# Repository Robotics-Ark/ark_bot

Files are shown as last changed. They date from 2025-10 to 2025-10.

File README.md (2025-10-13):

<h1 align="center">
🥳 Ark_Bot 🥳
</h1>

> **Handbook**  
> Version: `v1.0.0` • Date: `<2025-10>` • Author: `Harry Warriner / Ark`

---

<div align = "center">
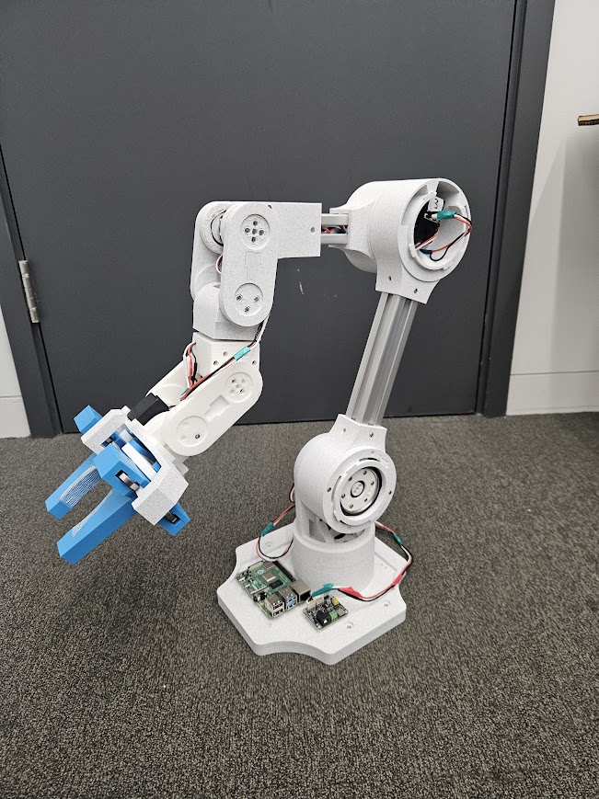
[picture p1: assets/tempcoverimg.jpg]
Cover Image

</div>

## Table of Contents

- [1. Overview](#1-overview)
- [2. Example Videos](#2-example-videos)
- [3. Bill of Materials](#3-bill-of-materials)
- [4. Required Tools](#4-required-tools)
- [5. List of 3D Parts](#5-list-of-3d-parts)

- [6. Specifications](#6-specifications)
- [7. Before You Start](#7-before-you-start)
- [8. Assembly Guide](#8-assembly-guide)

- [9. Motor Configuration](#9-motor-configuration)
- [10. Software Setup](#10-software-setup)
- [11. Calibration](#11-calibration)

- [12. Operation](#12-operation)
- [13. Troubleshooting](#13-troubleshooting)
- [14. FAQ](#14-faq)

---

## 1. Overview

**Purpose:** ArkBot is designed to be an affordable high strength, high accuracy robotic arm you can build at home.  
**Scope:** This handbook covers how to build ArkBot and how to get it running within the Ark Framework.

The ArkBot is a pick-and-place robotic arm designed to be affordable and easy to build at home. With the intention of demonstrating the <a href="https://github.com/Robotics-Ark/ark_framework">ark_framework's</a> capabilities. Comes complete with an accurate URDF file. <br>

<table align="center">
  <tr>
    <td align="center" style="border: none;">
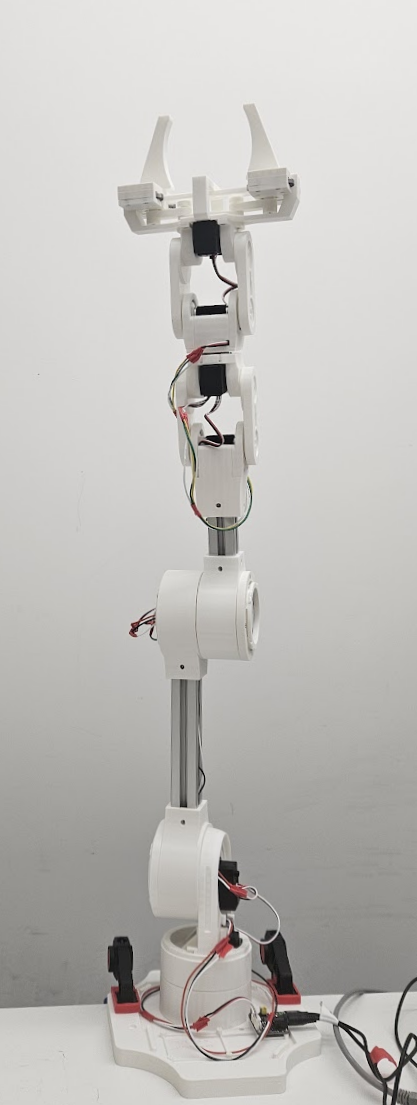
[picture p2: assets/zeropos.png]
      
    </td>
    <td align="center" style="border: none;">
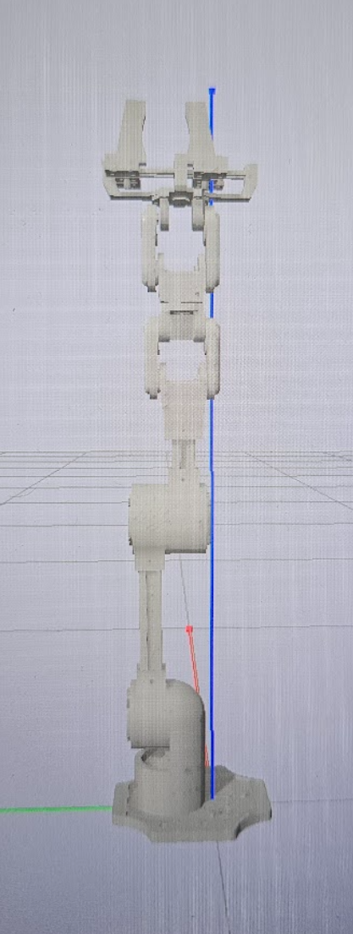
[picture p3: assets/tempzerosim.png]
      
    </td>
  </tr>
</table>

---

## 2. Example videos

<table>
<tr>
<td >Pick and Place</td>
<td >
  TPU Gripper Example
</td>
<td >Short IK Example</td>

</tr>
</table>

## 3. Bill of Materials.

The parts ordered from either side (amazon or cheapest) are the same parts, the difference is the time and price. The amazon links will come significantly faster whilst the others will take a while longer.
At the bottom though there are two different PLA filaments, the bambu or an equivalent high brand printer filament is reccomended, but if on a budget, the amazon ones will work fine.

| Totals | Amazon Total: | Cheapest Total: |
| --- | --- | --- |
| | £348.12 | £215.86 |

<hr>

<div align = "center" >

| Qty Needed | Name | Amazon Price | Amazon Link | Cheapest Price | Cheapest Link |
| --- | --- | --- | --- | --- | --- |
| 7 | ST 3215 Servos | £26.99 (x7)  | [Amazon](https://www.amazon.co.uk/Waveshare-Servo-Precision-Programmable-Switchable/dp/B0B6HSBRGF) | £20.10 (x7) | [Robotshop](https://uk.robotshop.com/products/waveshare-30kg-serial-bus-servo-high-precision-torque-w-360-deg-encoder) |
| 1 | Servo Bus Driver | £9.99 (x1) | [Amazon](https://www.amazon.co.uk/Waveshare-Integrates-Control-Applicable-Integrate/dp/B0CJ6TP3TP) | £4.80 (x1) | [PiHut](https://thepihut.com/products/serial-bus-servo-driver-board) |
| 36 | 693-2z (Tiny Bearings) | £9.89 (x2) | [Amazon](https://www.amazon.co.uk/sourcing-map-Groove-Bearing-Bearings/dp/B07FXVZ4W4) | £2.31 (x4) | [AliExpress](https://www.aliexpress.com/item/1005005858463502.html) |
| 12 | 6802-2RS (Medium Bearings)  | £9.79 (x2) | [Amazon](https://www.amazon.co.uk/dp/B07FXY8YHK) | £3.23 (x2) | [AliExpress](https://www.aliexpress.com/item/1005006082431261.html) |
| 5 | 6706-2RS (Big Bearings) | £12.19 (x1)  | [Amazon](https://www.amazon.co.uk/sourcing-map-30x37x4mm-Precision-Lubricated/dp/B0D6WJX2K5) | £1.27 (x5) | [AliExpress](https://www.aliexpress.com/item/1005003619960721.html) |
| 6 | 6810-2RS (Massive Bearings) | £26.29 (x1)  | [Amazon](https://www.amazon.co.uk/sourcing-map-50x65x7mm-Precision-Lubricated/dp/B0D728SYYT) | £10.39 (x1) | [AliExpress](https://www.aliexpress.com/item/32842423917.html) |
| 1 | 10cm 30x30 Aluminium Extr.  | £2.27 (x1) | [Amazon](https://www.aluminium-profile.co.uk/30x30-aluminium-profile-kjn990720/) | £2.27 (x1) | [Aluminium-Profile](https://www.aluminium-profile.co.uk/30x30-aluminium-profile-kjn990720/) |
| 1 | 20cm 30x30 Aluminium Extr.  | £3.35 (x1) | [Amazon](https://www.aluminium-profile.co.uk/30x30-aluminium-profile-kjn990720/) | £3.35 (x1) | [Aluminium-Profile](https://www.aluminium-profile.co.uk/30x30-aluminium-profile-kjn990720/) |
| 12 | M3 30x30 T-nuts (100) | £7.89 (x1) | [Amazon](https://www.amazon.co.uk/sourcing-map-Fastener-Aluminum-Accessories/dp/B0D5XK6SL1) | £3.46 (x1) | [AliExpress](https://www.aliexpress.com/item/1005005553086770.html) |
| 1 | Box of M3 Screws | £7.88 (x1) | [Amazon](https://www.amazon.co.uk/Assortment-Stainless-Replacement-Machine-Fastener/dp/B0B3MGZ7T2) | £7.88 (x1) | [Amazon](https://www.amazon.co.uk/Assortment-Stainless-Replacement-Machine-Fastener/dp/B0B3MGZ7T2) |
| 50 | Threaded Inserts (100) | £7.99 (x1) | [Amazon](https://www.amazon.co.uk/HANGLIFE-Threaded-Inserts-Printing-Components/dp/B0CS6VZYL8) | £0.98 (x1) | [AliExpress](https://www.aliexpress.com/item/1005008666672949.html) |
| 2 | 1kg of PLA | £20.99 (x2)  | [BambuLab](https://uk.store.bambulab.com/products/pla-basic-filament) | £9.99 (x2) | [Amazon](https://www.amazon.co.uk/PLA-Filament-Tolerance-Materials-Compatible/dp/B0DCJ7TTDK) |

</div>

---

## 4. Required Tools

This is a list of the most basic tools required to build the Ark_bot, additionally it is reccomended to have a drill and pliers, just to improve quality of assembly.

<div align="center">

| List of tools Required  |
| ----------------------- |
| 3D printer              |
| Soldering Iron          |
| 5mm 12v DC power supply |
| m3 Hex Key              |
| wire cutters            |
| electrical tape         |
| electrical wires        |
| Clamps                  |

</div>

---

## 5. List of 3D parts

> Release `v1.0.0` Parts List (Grouped by Subsystem)

<div align="center">

| **Base** | **Cyclodial Drive** | **Links** | **Claw** | **Limbs** |
| --- | --- | --- | --- | --- |
| 1 × Base | 2 × Motor Holders | 1 × Link 3 Body | 2 × Claw Connector | 2 × Limb Motor Side |
| 2 × Base Bearing Cover | 2 × Bearing Holder Disk (Exterior) | 2 × Link3 and 5 Motor Side | 1 × Claw Bottom Case | 2 × Limb Non Motor Side |
| 1 × Base Motor Holder | 2 × Cyclodial Drive Exterior | 2 × Link3 and 5 Side | 1 × Claw Runners | |
| 1 × Joint 1 Base | 2 × Cyclodial Drive Exterior Top | 1 × Link4 | 2 × Claw Body | |
| 1 × Joint 1 Connector to Joint 2 | 1 × Cyclodial Drive Other Half | 1 × Link5 Body | 4 × Claw Runner Clamp | |
| | 3 × Eccentric Rod Motor Connector | | 2 × Claw Link | |
| | 18 × Internal Cyclodial Drive Spacer | | 2 × Finger | |
| | 6 × Cyclodial Disk | | 1 × Claw Motor Driver | |
| | 3 × Cyclodial Driver Interior Top | | 2 × Claw Motor Holder Link Pin | |
| | 3 × Eccentric Rod Middle | | 2 × Claw Link Motor | |
| | 3 × Eccentric Rod Top | | 2 × Claw Link Cap | |
| | 3 × Cyclodial Driver Interior Bottom | | | |

---

**Total Parts: 86**

</div>

---

## 6. Specifications

| Parameter | Value  |
| --- | --- |
| Reach | 1 m |
| Weight | 2.6 kg |
| Payload | 1.8kg  |
| DOF | 6 |
| Input Voltage | DC12V  |

---

## 7. Before You Start

When 3D printing, the Cyclodial Disks, ensure that the diameter of the 6 holes on the outside are exactly 12mm in diamter, and that the disk fits near perfectly in the exterior.

<div align = "center">
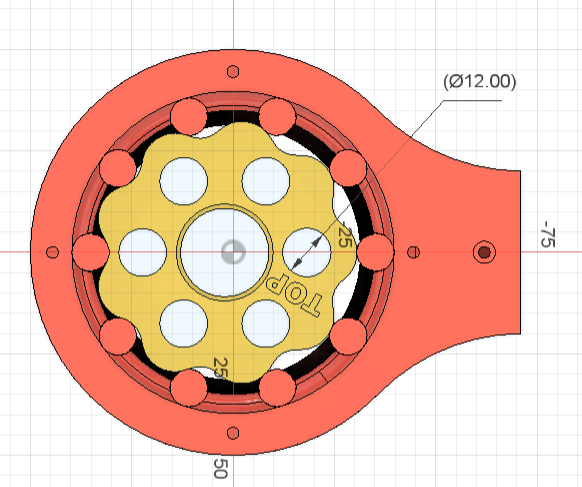
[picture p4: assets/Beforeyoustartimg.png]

</div>

The better the fit the more accurate the final positioning will be.

> This is the only note with the 3D prininting, as long as these two parts work. Everything else can be printed on random settings, of course the higher the infill the stronger the final parts.

---

## 8. Assembly Guide

> ⏱ **Total time:** <estimate, 120 minutes>  
> 🧰 **Skill level:** Intermediate
<div align="center">
  
Assembly (https://www.youtube.com/watch?v=Kuk4pC0EaEw)

If clicking the above video did not work, click [here](https://www.youtube.com/watch?v=Kuk4pC0EaEw)

</div>
---

## 9. Motor Configuration

Connect the indivual motor to the driver board.

Go to the configuration.py file in arkbot. <a href="arkbot\Configuration.py">Config file</a>

Make sure the config is correct in the file:

```python
if __name__ == "__main__":
    DEVICENAME = "COM7"       # or "/dev/ttyUSB0"
    BAUDRATE   = 1_000_000
```

Then run the program, it will tell you the ID number of the motor, if this is not correct, change it to the number associated to that motor.

---

## 10. Software Setup

### Ark Framework

Go to the Ark Framework repo and follow the instructions there.

Make sure Ark Registry is running.

Make sure arkbot.py is also running (in a different terminal)

Then use the jupyter notebook in tests, if using sim, make sure sim_node.py is running. And that sim=true in the config of the jupyter notebook.

**Configure:**
Make sure the port is correct in the .yaml file.

```json
{
  real_config:
        port: "/dev/ttyACM0"
        baudrate: 1000000
}
```

---

## 11. Calibration

You should be able to carefully move the cyclodial drives and the motors when powered off. Move ArkBot so that it is completly facing upwards, and plug it in. Run the configuration.py file, and when promted set all the midpoint positions.

Power cycle the robotic arm, and run the configuration code, and when promted go to output and read the current ticks of all the motors. These then need to be put into the arkbot.yaml file:

```json
home_ticks:
          {
            "1": 2800,
            "2": 2431,
            "3": 2093,
            "4": 2050,
            "5": 2059,
            "6": 2020,
            "7": 1011,
          }
```

Next is the home loop configuration. The robotic arm must start from the position below. (Only matters for the first 3 motors) These motors rotate multiple times due to the gear ratio. Therefore the loops to get the [0,0,0,...] position must also be inputted:

```json
home_loops: {
    "1": 0, "2": 3, "3": 3, "4": 0, "5": 0, "6": 0, "7": 0
    }
```

Now run the jupyter notebook and send it to [0,0,0,...] if it goes straight up then the calibration was a succsess.

Cover Image

> ✅ **Pass criteria:** When sent to [0,0,0,...] it goes straight up

---

## 12. Operation

- Ensure that it is in the starting position.
- Power on and send to home.
- If succseful, enjoy using ArkBot!

---

## 13. Troubleshooting

| Symptom | Possible Causes | Fix |
| --- | --- | --- |
| Won’t power on | 12V Cable Not Plugged in | Plug it in |
| Jittery motion | Cyclodial disks not correct size | Reprint to size |
| Massive Backlash | Plastic could have worn and snapped | Reprint parts |

---

## 14. FAQ

**Q:**
**A:**

**Q:**
**A:**

---

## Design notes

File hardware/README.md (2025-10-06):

# 3D Assets

## Excel Spreadsheet
There is an Excel spreadsheet which can be downloaded and used as a checklist for all the 3D models

## External 3D assets used
Links to any websites which was used for external 3D assets.

### Traceparts
Used for Aluminium Profile Extrusions
<!-- *[TraceParts](https://www.traceparts.com/en)* -->

<!-- *[20x20 Profile](https://www.traceparts.com/en/product/dongguan-forrun-hardware-co-ltd-20-series-aluminium-alloy-profiles-20x20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)* -->
*[30x30 Profile](https://www.traceparts.com/en/product/dongguan-forrun-hardware-co-ltd-30-series-aluminium-alloy-profiles-30x30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)*

### Astbearings
USed for Bearings

*[6706-2RS Bearing](https://www.astbearings.com/catalog/root/6706-2RS)*

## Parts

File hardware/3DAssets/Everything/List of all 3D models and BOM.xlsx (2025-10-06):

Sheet: 3D models
Release V1.0
 | Quanity | Name of File
 | 1 | Base
 | 2 | Base Bearing Cover
 | 1 | Base Motor Holder
 | 1 | Joint 1 Base
 | 1 | Joint 1 Connector to Joint 2
 | 2 | Motor Holders
 | 2 | Bearing Holder Disk for cyclodial Drive exterior | Bill of Materials In the other sheet
 | 2 | Cyclodial Drive Exterior
 | 2 | Cyclodial Drive Exterior Top
 | 1 | Cyclodial Drive Other Half
 | 3 | Eccentric Rod Motor Connector
 | 18 | Internal Cyclodial drive Spacer
 | 6 | Cyclodial Disk
 | 3 | Cyclodial Driver Interior Top
 | 3 | Eccentric Rod Middle
 | 3 | Eccentric Rod Top
 | 3 | Cyclodial Driver Interior Bottom
 | 1 | Link 3 Body
 | 2 | Link3 and 5 Motor Side
 | 2 | Link3 and 5 Side
 | 1 | Link4
 | 1 | Link5 Body
 | 2 | Claw Connector
 | 1 | Claw Bottom Case
 | 1 | Claw Runners
 | 2 | Claw Body
 | 4 | Claw Runner Clamp
 | 2 | Claw Link
 | 2 | Finger
 | 1 | Claw Motor Driver
 | 2 | Claw Motor Holder Link PIn
 | 2 | Claw Link Motor
 | 2 | Claw Link Cap
 | 2 | Limb Motor Side
 | 2 | Limb Non Motor Side
Total parts: | 86

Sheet: Bill of Materials
 |  |  | Amazon |  |  |  |  | Cheapest Found
 |  | Quantity in link | Name | Price | Link | Quantiy needed | Quantity in link | Name | Price | Link | Quantity Needed
7 | ST 3215 Servos | 1 | ST 3215 Servos | £26.99 | https://www.amazon.co.uk/Waveshare-Servo-Precision-Programmable-Switchable/dp/B0B6HSBRGF?s=industrial | 7 | 1 | ST 3215 Servos | £20.10 | https://uk.robotshop.com/products/waveshare-30kg-serial-bus-servo-high-precision-torque-w-360-deg-encoder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 | 7
1 | Servo Bus Driver | 1 | Servo Bus Driver | £9.99 | https://www.amazon.co.uk/Waveshare-Integrates-Control-Applicable-Integrate/dp/B0CJ6TP3TP | 1 | 1 | Servo Bus Driver | £4.80 | https://thepihut.com/products/serial-bus-servo-driver-board | 1
36 | 693-2z(or zz) (Tiny Bearings) | 20 | 693-2z(or zz) (Tiny Bearings) | £9.89 | https://www.amazon.co.uk/sourcing-map-Groove-Bearing-Bearings/dp/B07FXVZ4W4?s=amazon-devices | 2 | 10 | 693-2z(or zz) (Tiny Bearings) | £2.31 | https://www.aliexpress.com/item/1005005858463502.html?curPageLogUid=vG9asOPYtleS | 4
12 | 6802-2RS (Medium Bearings | 10 | 6802-2RS (Medium Bearings | £9.79 | https://www.amazon.co.uk/dp/B07FXY8YHK?ref_=ppx_hzsearch_conn_dt_b_fed_asin_title_4&th=1 | 2 | 10 | 6802-2RS (Medium Bearings | £3.23 | https://www.aliexpress.com/item/1005006082431261.html?curPageLogUid=MpFagQTCKDh6 | 2
5 | 6706-2RS (Big Bearings) | 5 | 6706-2RS (Big Bearings) | £12.19 | https://www.amazon.co.uk/sourcing-map-30x37x4mm-Precision-Lubricated/dp/B0D6WJX2K5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 | 1 | 1 | 6706-2RS (Big Bearings) | £1.27 | https://www.aliexpress.com/item/1005003619960721.html?curPageLogUid=VV2sZ14YRMKX | 5
6 | 6810-2RS (Massive Bearings) | 10 | 6810-2RS (Massive Bearings) | £26.29 | https://www.amazon.co.uk/sourcing-map-50x65x7mm-Precision-Lubricated/dp/B0D728SYYT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 | 1 | 10 | 6810-2RS (Massive Bearings) | £10.39 | https://www.aliexpress.com/item/32842423917.html?curPageLogUid=EFcuFxcUSFh2 | 1
1 | 10cm 30x30 Alluminum extrusion | 1 | 10cm 30x30 Alluminum extrusion | £2.27 | https://www.aluminium-profile.co.uk/30x30-aluminium-profile-kjn990720/ | 1 | 1 | 10cm 30x30 Alluminum extrusion | £2.27 | https://www.aluminium-profile.co.uk/30x30-aluminium-profile-kjn990720/ | 1
1 | 20cm 30x30 Alluminum extrusion | 1 | 20cm 30x30 Alluminum extrusion | £3.35 | https://www.aluminium-profile.co.uk/30x30-aluminium-profile-kjn990720/ | 1 | 1 | 20cm 30x30 Alluminum extrusion | £3.35 | https://www.aluminium-profile.co.uk/30x30-aluminium-profile-kjn990720/ | 1
12 | M3 30x30 T-nuts | 100 | M3 30x30 T-nuts | £7.89 | https://www.amazon.co.uk/sourcing-map-Fastener-Aluminum-Accessories/dp/B0D5XK6SL1 | 1 | 20 | M3 30x30 T-nuts | £3.46 | https://www.aliexpress.com/item/1005005553086770.html?curPageLogUid=1GgLfjFOVcWH | 1
1 | Box of generic M3 screws | 1 | Box of generic M3 screws | £7.88 | https://www.amazon.co.uk/Assortment-Stainless-Replacement-Machine-Fastener/dp/B0B3MGZ7T2 | 1 | 1 | Box of generic M3 screws | £7.88 | https://www.amazon.co.uk/Assortment-Stainless-Replacement-Machine-Fastener/dp/B0B3MGZ7T2 | 1
50 | Threaded inserts | 100 | Threaded inserts | £7.99 | https://www.amazon.co.uk/HANGLIFE-Threaded-Inserts-Printing-Components/dp/B0CS6VZYL8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 | 1 | 50 | Threaded inserts | £0.98 | https://www.aliexpress.com/item/1005008666672949.html?curPageLogUid=AIubewLqcBkO | 1
2 | 1kg of PLA | 1 | 1kg of PLA | £20.99 | https://uk.store.bambulab.com/products/pla-basic-filament?id=40589883768892 | 2 | 1 | 1kg of PLA | £9.99 | https://www.amazon.co.uk/PLA-Filament-Tolerance-Materials-Compatible/dp/B0DCJ7TTDK | 2
 |  |  |  | Total Price from amazon |  |  |  |  | Total Price from cheapsource
 |  |  |  | £348.12 |  |  |  |  | £215.86

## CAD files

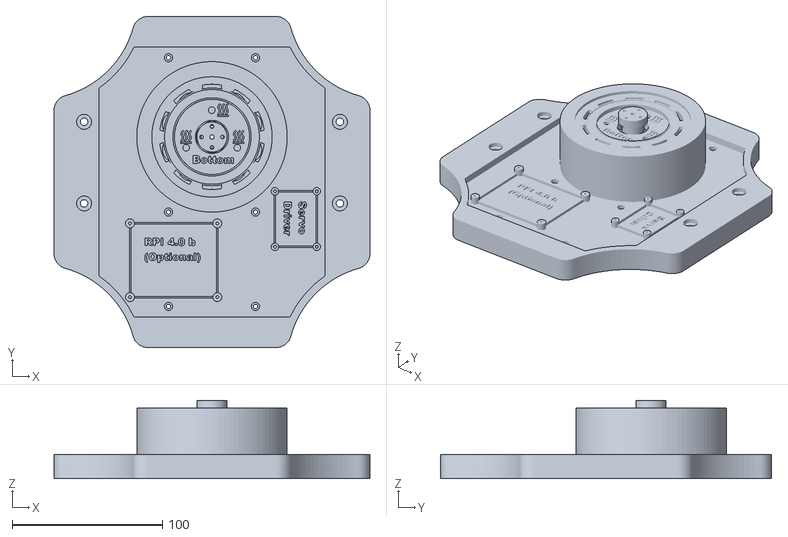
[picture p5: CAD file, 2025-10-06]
arkbot/meshes/collision/base_link.stl
210.0 x 220.0 x 52.0

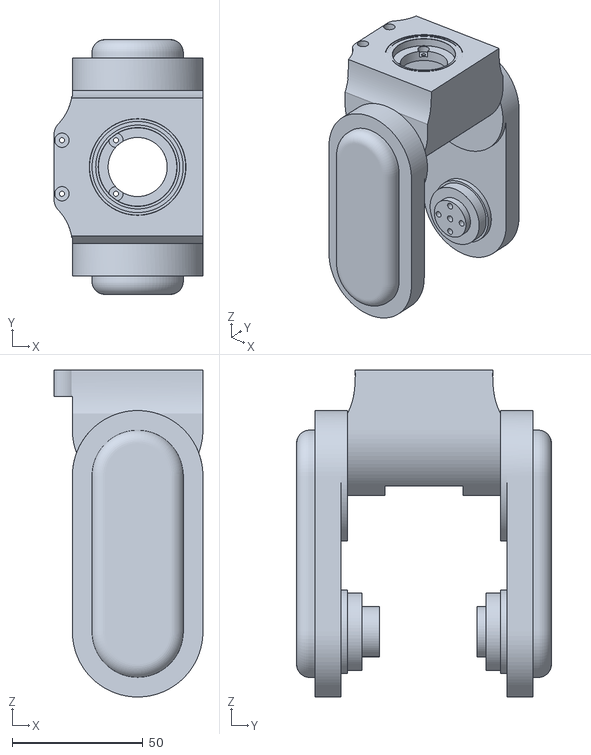
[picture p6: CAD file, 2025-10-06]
arkbot/meshes/visual/link4_v2_1.stl
57.0 x 97.6 x 125.2

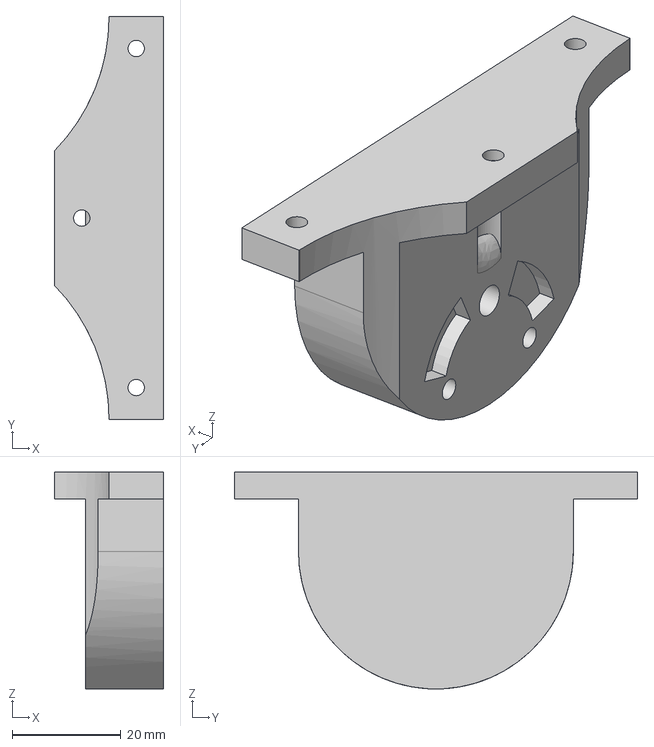
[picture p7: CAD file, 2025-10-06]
hardware/3DAssets/Everything/Claw Connector.step
20.0 x 74.0 x 39.8 mm

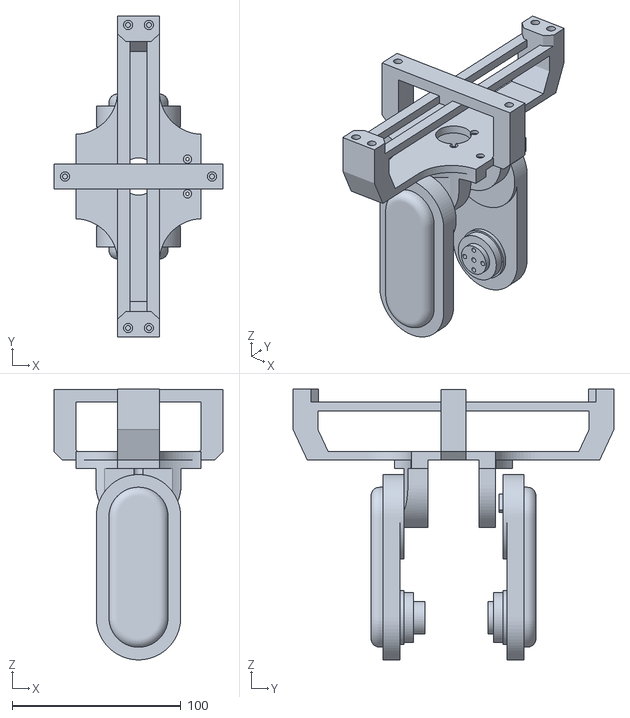
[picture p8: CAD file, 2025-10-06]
hardware/URDF/meshes/collision/Hand_v2_1.stl
100.0 x 190.0 x 160.2

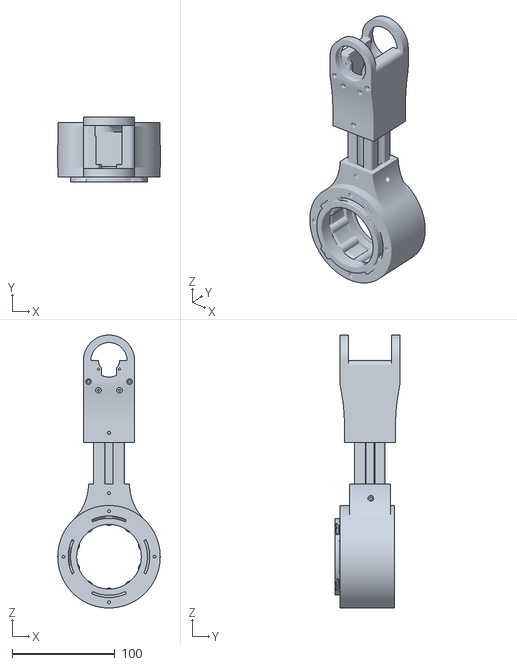
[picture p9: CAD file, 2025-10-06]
hardware/URDF/meshes/visual/link3_v2_1.stl
100.0 x 63.4 x 266.3

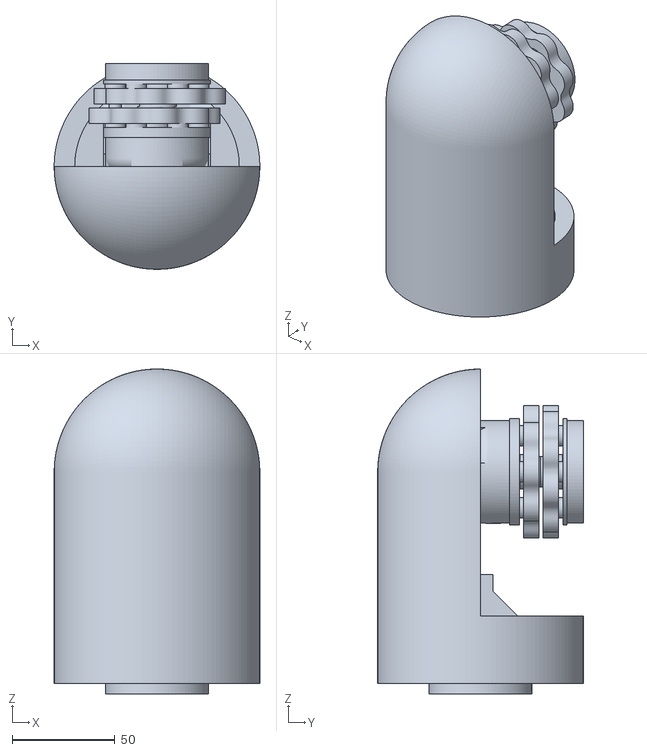
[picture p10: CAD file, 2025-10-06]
arkbot/meshes/collision/Link1_v2_1.stl
100.0 x 100.0 x 158.0

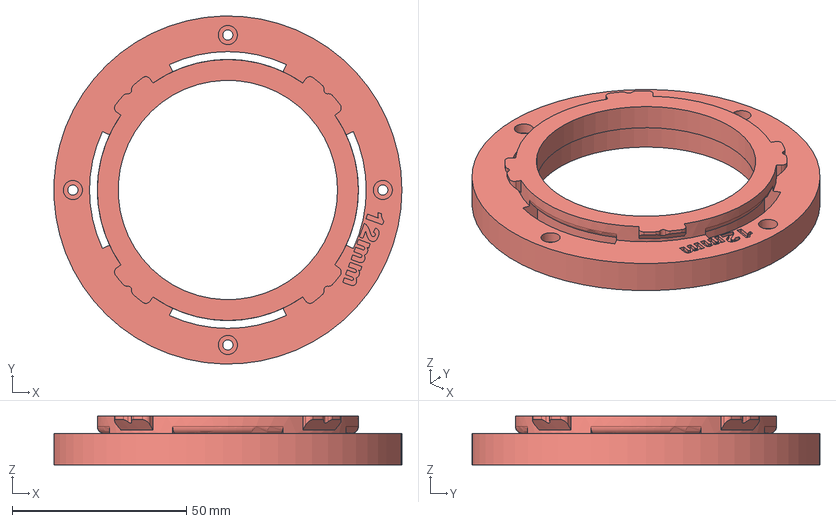
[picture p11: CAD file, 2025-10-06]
hardware/3DAssets/Everything/Cyclodial Drive Exterior Top.step
99.9 x 100.0 x 14.0 mm

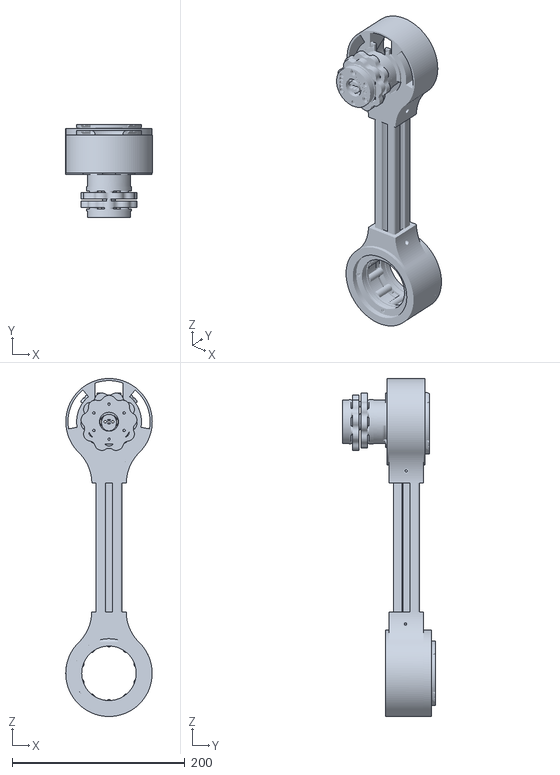
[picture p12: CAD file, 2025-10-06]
hardware/URDF/meshes/collision/link2_v2_1.stl
100.1 x 108.1 x 391.1

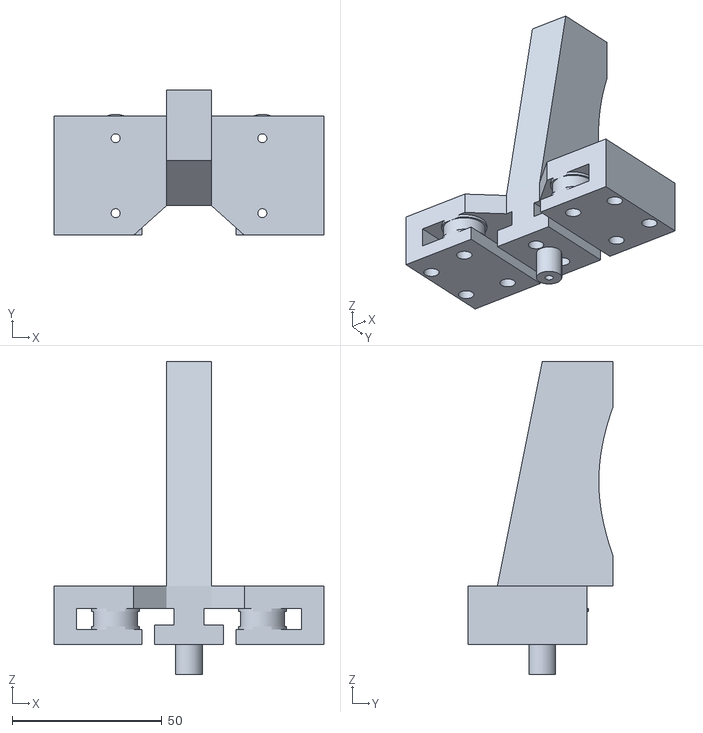
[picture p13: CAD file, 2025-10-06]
hardware/URDF/meshes/visual/finger_v2__1__1.stl
90.0 x 48.6 x 104.5

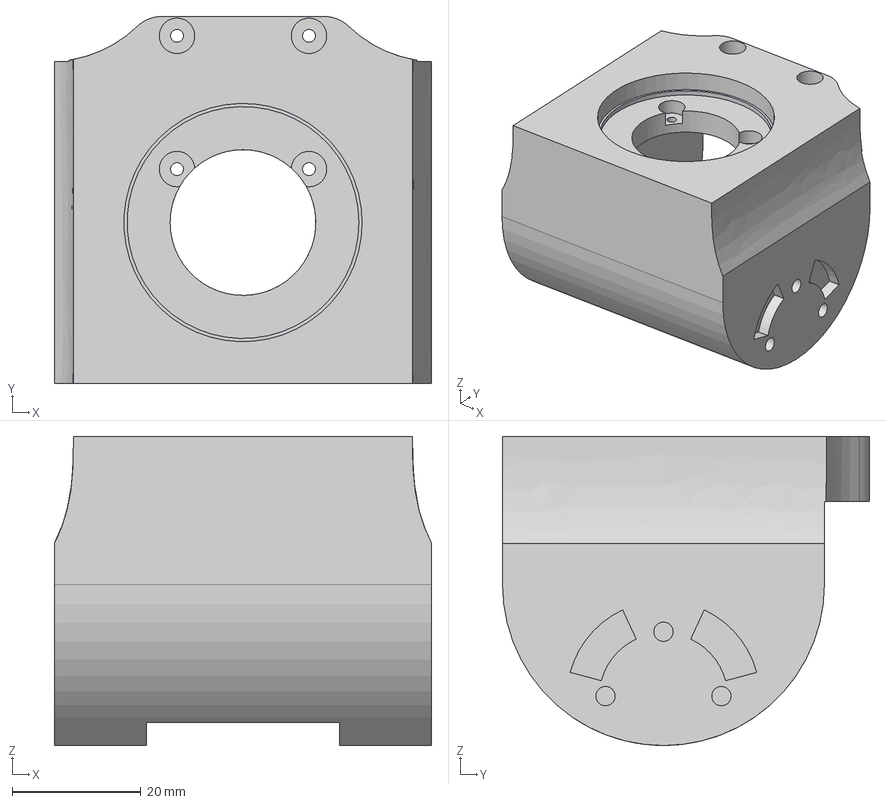
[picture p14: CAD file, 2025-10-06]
hardware/3DAssets/Everything/Link4.step
58.6 x 57.0 x 48.0 mm

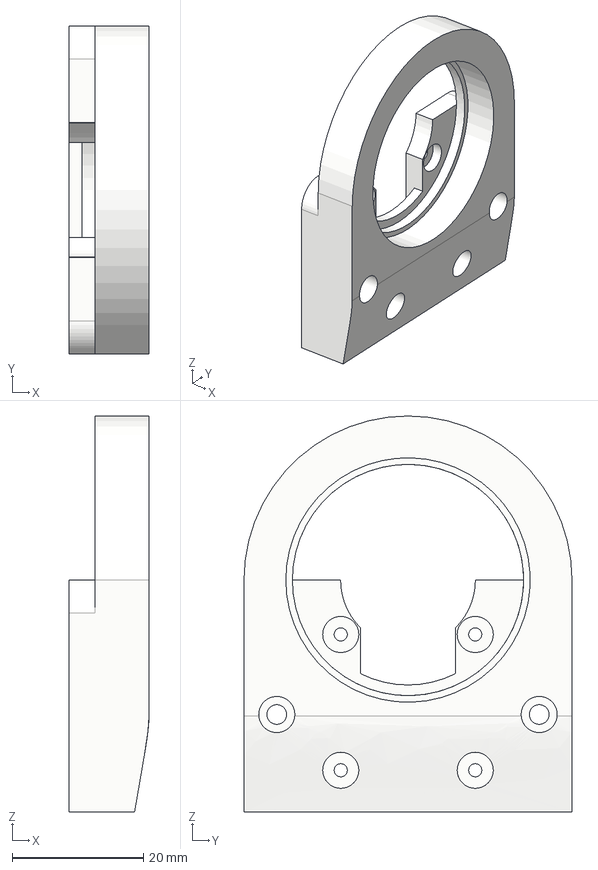
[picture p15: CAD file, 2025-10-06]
hardware/3DAssets/Everything/Link3 and 5 Motor Side.step
12.2 x 50.0 x 60.4 mm

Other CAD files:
arkbot/meshes/collision/finger_v2_1.stl
arkbot/meshes/collision/link5_v2_1.stl
arkbot/meshes/visual/finger_v2_1.stl
arkbot/meshes/visual/link5_v2_1.stl
hardware/3DAssets/Everything/Base Bearing Cover.step
hardware/3DAssets/Everything/Base Motor Holder.step
hardware/3DAssets/Everything/Base.step
hardware/3DAssets/Everything/Bearing Holder Disk for cyclodial Drive exterior.step
hardware/3DAssets/Everything/Claw Body.step
hardware/3DAssets/Everything/Claw Bottom Case.step
hardware/3DAssets/Everything/Claw Link Cap.step
hardware/3DAssets/Everything/Claw Link Motor.step
hardware/3DAssets/Everything/Claw Link.step
hardware/3DAssets/Everything/Claw Motor Driver.step
hardware/3DAssets/Everything/Claw Motor Holder Link PIn.step
hardware/3DAssets/Everything/Claw Runner Clamp.step
hardware/3DAssets/Everything/Claw Runners.step
hardware/3DAssets/Everything/Cyclodial Disk.step
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

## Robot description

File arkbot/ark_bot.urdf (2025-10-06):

<?xml version="1.0" ?>
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
<robot name="ArkBot">
  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
  <link name="base_link">
    <inertial>
      <origin rpy="0 0 0" xyz="1.627798830346459e-05 0.038788043101890254 0.012657311430416793"/>
      <mass value="5.279041030398897"/>
      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
    </inertial>
    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
  </link>
  <link name="Link1">
    <inertial>
      <origin rpy="0 0 0" xyz="-8.789698917545885e-07 -0.00209324666321261 0.06034546164127977"/>
      <mass value="3.55259145758094"/>
      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
    </inertial>
    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
  </link>
  <link name="link2">
    <inertial>
      <origin rpy="0 0 0" xyz="4.5648705801939816e-05 0.017680813699606 0.1474793511706172"/>
      <mass value="4.329966529786294"/>
      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
    </inertial>
    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
  </link>
  <link name="link3">
    <inertial>
      <origin rpy="0 0 0" xyz="-1.847661592824805e-05 -0.02606315938822895 0.06299775440518512"/>
      <mass value="3.239056584746587"/>
      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
    </inertial>
    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
  </link>
  <link name="link4">
    <inertial>
      <origin rpy="0 0 0" xyz="0.0005635271959570314 0.023726686595274354 0.04715061702801071"/>
      <mass value="1.7025158483719638"/>
      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
    </inertial>
    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
  </link>
  <link name="link5">
    <inertial>
      <origin rpy="0 0 0" xyz="7.240975234131843e-05 0.000377618306209547 0.02592927980852644"/>
      <mass value="0.6135827464240919"/>
      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
    </inertial>
    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
  </link>
  <link name="Hand">
    <inertial>
      <origin rpy="0 0 0" xyz="-7.861406339096539e-05 0.02320812243170746 0.06508389882077914"/>
      <mass value="2.2197201602974554"/>
      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
    </inertial>
    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
  </link>
  <link name="finger1">
    <inertial>
      <origin rpy="0 0 0" xyz="-0.004999628701543117 -0.015384046201054255 0.015310449682612193"/>
      <mass value="0.653538155273753"/>
      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
    </inertial>
    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
  </link>
  <link name="finger2">
    <inertial>
      <origin rpy="0 0 0" xyz="-0.00499962868826751 0.015383111119019108 0.015310449682611749"/>
      <mass value="0.6535381552737535"/>
      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
    </inertial>
    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
  </link>
  <joint name="Revolute 1" type="continuous">
    <origin rpy="0 0 0" xyz="0.0 0.06 0.046"/>
    <parent link="base_link"/>
    <child link="Link1"/>
    <axis xyz="0.0 0.0 -1.0"/>
  </joint>
  <joint name="Revolute 2" type="revolute">
    <origin rpy="0 0 0" xyz="-0.0 0.0 0.103"/>
    <parent link="Link1"/>
    <child link="link2"/>
    <axis xyz="-0.0 1.0 0.0"/>
    <limit effort="100" lower="-2.268928" upper="2.268928" velocity="100"/>
  </joint>
  <joint name="Revolute 3" type="revolute">
    <origin rpy="0 0 0" xyz="9.9e-05 0.001867 0.291081"/>
    <parent link="link2"/>
    <child link="link3"/>
    <axis xyz="-0.0 -1.0 -0.0"/>
    <limit effort="100" lower="-2.70526" upper="2.70526" velocity="100"/>
  </joint>
  <joint name="Revolute 4" type="revolute">
    <origin rpy="0 0 0" xyz="0.0 -0.046977 0.191308"/>
    <parent link="link3"/>
    <child link="link4"/>
    <axis xyz="-0.0 1.0 -0.0"/>
    <limit effort="100" lower="-2.356194" upper="2.356194" velocity="100"/>
  </joint>
  <joint name="Revolute 5" type="continuous">
    <origin rpy="0 0 0" xyz="0.0 0.0238 0.096239"/>
    <parent link="link4"/>
    <child link="link5"/>
    <axis xyz="0.0 -0.0 -1.0"/>
  </joint>
  <joint name="Revolute 6" type="revolute">
    <origin rpy="0 0 0" xyz="0.0 -0.0231 0.045761"/>
    <parent link="link5"/>
    <child link="Hand"/>
    <axis xyz="0.0 1.0 -0.0"/>
    <limit effort="100" lower="-2.356194" upper="2.356194" velocity="100"/>
  </joint>
  <joint name="Slider 7" type="prismatic">
    <origin rpy="0 0 0" xyz="0.005124 0.1038 0.127614"/>
    <parent link="Hand"/>
    <child link="finger1"/>
    <axis xyz="0.0 -1.0 0.0"/>
    <limit effort="100" lower="0.0" upper="0.0425" velocity="100"/>
  </joint>

  <joint name="Slider 8" type="prismatic">
    <origin rpy="0 0 0" xyz="0.005124 -0.0562 0.127614"/>
    <parent link="Hand"/>
    <child link="finger2"/>
    <axis xyz="0.0 -1.0 0.0"/>
    <limit effort="100" lower="-0.0425" upper="0.0" velocity="100"/>
    <mimic joint="Slider 7" multiplier="-1.0" />
  </joint>

</robot>

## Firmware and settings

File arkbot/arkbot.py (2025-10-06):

from typing import Any, Dict
from dataclasses import dataclass
from enum import Enum
import numpy as np

from ark.client.comm_infrastructure.base_node import main
from ark.system.component.robot import Robot
from ark.system.driver.robot_driver import RobotDriver
from ark.system.pybullet.pybullet_robot_driver import BulletRobotDriver
from ark.tools.log import log
from arktypes import joint_state_t, joint_group_command_t, task_space_command_t
from arktypes.utils import unpack



@dataclass
class Drivers(Enum):
    PYBULLET_DRIVER = BulletRobotDriver
    try:
        from ark_bot_driver import ArkBotDriver  
        DRIVER = ArkBotDriver
    except ImportError:
        log.warn("ArkBotDriver is failing")
    

class ArkBot(Robot):
    def __init__(self, name: str, global_config: Dict[str, Any] = None, driver: RobotDriver = None):
        super().__init__(name=name, global_config=global_config, driver=driver)
    
        self.joint_group_command_ch = f"{self.name}/joint_group_command"
        self.cartesian_position_control_ch = f"{self.name}/cartesian_command"
        if self.sim:
            self.joint_group_command_ch += "/sim"
            self.cartesian_position_control_ch += "/sim"
       
        self.create_subscriber(self.joint_group_command_ch, joint_group_command_t, self._joint_group_command_cb)
        self.create_subscriber(self.cartesian_position_control_ch, task_space_command_t, self._cartesian_position_cb)
        
        self.joint_states_pub = f"{self.name}/joint_states" + ("/sim" if self.sim else "")
        self.component_channels_init({ self.joint_states_pub: joint_state_t })

        self.joint_group_command = None
        self.cartesian_position_control_command = None

    def control_robot(self):
        if self.joint_group_command:
            print(self.joint_group_command)
            group_name = self.joint_group_command["name"]
            ordered_names = list(self.joint_groups[group_name]["joints"])
            ordered_vals = self.joint_group_command["cmd"]
            cmd_dict = dict(zip(ordered_names, ordered_vals))
            control_mode = self.joint_groups[group_name]["control_mode"]
            self.control_joint_group(control_mode=control_mode, cmd=cmd_dict)
            self.joint_group_command = None

        if self.cartesian_position_control_command:
            group_name = self.cartesian_position_control_command["name"]
            control_mode = self.joint_groups[group_name]["control_mode"]
            ee_idx = self.config.get("ee_index", 5) 
            self._driver.pass_cartesian_control_cmd(
                control_mode,
                position=self.cartesian_position_control_command["position"],
                quaternion=self.cartesian_position_control_command["quaternion"],
                end_effector_idx=ee_idx,
                gripper=self.cartesian_position_control_command.get("gripper", None),
            )
            self.cartesian_position_control_command = None

    def get_state(self) -> Dict[str, Any]:
        joints = self.get_joint_positions()
        return {"joint_positions": joints}

    def pack_data(self, state: Dict[str, Any]) -> Dict[str, Any]:
        joint_state = state["joint_positions"]

        msg = joint_state_t()
        msg.n = len(joint_state)
        msg.name = list(joint_state.keys())
        msg.position = list(joint_state.values())
        msg.velocity = [0.0] * msg.n
        msg.effort   = [0.0] * msg.n

        # print(joint_state)
        return { self.joint_states_pub: msg }

    def _joint_group_command_cb(self, t, ch, msg):
        cmd, name = unpack.joint_group_command(msg)
        self.joint_group_command = {"cmd": cmd, "name": name}

    def _cartesian_position_cb(self, t, ch, msg):
        name, position, quaternion, gripper = unpack.task_space_command(msg)
        self.cartesian_position_control_command = {
            "name": name, "position": position, "quaternion": quaternion, "gripper": gripper
        }

CONFIG_PATH = "arkbot.yaml"
if __name__ == "__main__":
    name = "arkbot"
    from ark_bot_driver import ArkBotDriver
    driver = ArkBotDriver(name, CONFIG_PATH, sim=False)
    main(ArkBot, name, CONFIG_PATH, driver)

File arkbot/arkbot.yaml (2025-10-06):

robots:
  - name: "arkbot"
    config:
      source: "urdf"
      urdf_path: "ark_bot.urdf"
      class_dir: "../arkbot"
      frequency: 240
      base_position: [0, 0, 0]
      base_orientation: [0, 0, 0, 1] # x, y, z, w
      use_fixed_base: true

      initial_configuration:
        - 0.0 # Revolute 1
        - -2.0 # Revolute 2
        - 0.0 # Revolute 3
        - 0.0 # Revolute 4
        - 0.0 # Revolute 5
        - 0.0 # Revolute 6
        - 0.0 # Slider 7
        - 0.0 # slider 8

      ee_index: 5

      joint_groups:
        arm:
          control_mode: "position"
          joints:
            - "Revolute 1"
            - "Revolute 2"
            - "Revolute 3"
            - "Revolute 4"
            - "Revolute 5"
            - "Revolute 6"
        gripper:
          control_mode: "velocity"
          joints:
            - "Slider 7"
        all:
          control_mode: "position"
          joints:
            - "Revolute 1"
            - "Revolute 2"
            - "Revolute 3"
            - "Revolute 4"
            - "Revolute 5"
            - "Revolute 6"
            - "Slider 7"

      real_config:
        port: "/dev/ttyACM0"
        baudrate: 1000000

        # IMPORTANT: joint_order must match the names used elsewhere , in the SAME order as motor_ids
        motor_ids: [1, 2, 3, 4, 5, 6, 7, 8]
        joint_order:
          [
            "Revolute 1",
            "Revolute 2",
            "Revolute 3",
            "Revolute 4",
            "Revolute 5",
            "Revolute 6",
            "Slider 7",
            "Slider 8",
          ]

        gear_ratios:
          {
            "1": 9.0,
            "2": 9.0,
            "3": 9.0,
            "4": 1.0,
            "5": 1.0,
            "6": 1.0,
            "7": 9.0,
          }

        motor_orientations:
          { "1": -1, "2": -1, "3": -1, "4": 1, "5": 1, "6": -1, "7": 1 }
        home_ticks:
          {
            "1": 2800,
            "2": 2431,
            "3": 2093,
            "4": 2050,
            "5": 2059,
            "6": 2020,
            "7": 1011,
          }
        home_loops: { "1": 0, "2": 3, "3": 3, "4": 0, "5": 0, "6": 0, "7": 0 }
        ticks_per_turn: 4096

        speed_default: 190
        acc_default: 50
        motor_speeds: { "7": 1000 }

        gripper:
          # Use the same name that appears in joint_groups
          name: "finger1"
          id: 9
          min_width_m: 0.0
          max_width_m: 0.08
          min_ticks: 1000
          max_ticks: 3000
          speed: 1000
          acc: 30

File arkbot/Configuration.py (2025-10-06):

#!/usr/bin/env python3

from servopkg.bus import ServoBus

def scan_servos(port: str, baudrate: int, max_id: int = 20):
    bus = ServoBus(port, baudrate)
    sdk = bus.sdk
    found = []
    try:
        for sid in range(0, max_id + 1):
            model, comm, err = sdk.ping(sid)
            if comm == 0 and err == 0 and model is not None:
                print(f"Servo found at ID {sid} (model {model})")
                found.append(sid)
    finally:
        bus.close()
    return found

def prompt_int(prompt: str, lo: int, hi: int) -> int:
    while True:
        s = input(prompt).strip()
        try:
            v = int(s)
            if lo <= v <= hi:
                return v
            print(f"Enter a number between {lo} and {hi}.")
        except ValueError:
            print("Please enter a valid integer.")

if __name__ == "__main__":
    DEVICENAME = "COM7"       # or "/dev/ttyUSB0"
    BAUDRATE   = 1_000_000

    # 1) Scan
    ids = scan_servos(DEVICENAME, BAUDRATE)
    if ids:
        print("\nConnected servo IDs:", ids)
    else:
        print("\nNo servos detected.")

    # --- NEW: optional midpoint action on all detected IDs ---
    if ids:
        mid_ans = input("Press 'm' to set ALL detected servos to midpoint (or Enter to skip): ").strip().lower()
        if mid_ans == "m":
            bus = ServoBus(DEVICENAME, BAUDRATE)
            sdk = bus.sdk
            try:
                for sid in ids:
                    ok = sdk.DefineMiddle(sid)
                    if ok:
                        print(f"✅ Midpoint defined on ID {sid}")
                    else:
                        print(f"❌ Failed to define midpoint on ID {sid}")
            finally:
                bus.close()
        print()  # spacer
    # ---------------------------------------------------------

    # 2) Ask to change ID
    ans = input("Change ID? (y/n): ").strip().lower()
    if ans != "y":
        print("Ok")
        raise SystemExit(0)

    current_id = prompt_int("Enter current ID to change: ", 0, 253)
    new_id     = prompt_int("Enter NEW ID: ", 0, 253)

    # 3) Open bus once and change via SDK
    bus = ServoBus(DEVICENAME, BAUDRATE)
    sdk = bus.sdk
    try:
        # Optional: sanity check the current ID exists
        _, comm, err = sdk.ping(current_id)
        if comm != 0 or err != 0:
            print(f"ID {current_id} is not responding; aborting.")
            raise SystemExit(1)

        res = sdk.ChangeID(current_id, new_id)
        if res is None:
            print(f"ID changed to {new_id}. Verifying...")
            _, comm2, err2 = sdk.ping(new_id)
            if comm2 == 0 and err2 == 0:
                print(f"Verified: servo responds at ID {new_id}.")
            else:
                print("⚠️ ID write may have succeeded, but ping to new ID failed.")
        else:
            # ChangeID returns an error string on failure
            print("Failed to change ID:", res)
    finally:
        bus.close()

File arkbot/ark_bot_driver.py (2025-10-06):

# ark_bot_driver.py
from typing import Dict, Any, List
import math
import time
import threading

from ark.system.driver.robot_driver import RobotDriver
from ark.tools.log import log

# ---- Your servo SDK ----
from servopkg import PortHandler, sts  # expects .ReadAbsPos, ChangeMode, send_goal, ...
# --- imports unchanged ---

_TWO_PI = 2.0 * math.pi

class ArkBotDriver(RobotDriver):
    def __init__(self, component_name: str, component_config: Dict[str, Any] = None, sim: bool = False):
        super().__init__(component_name, component_config, sim)
        rc = self.config["real_config"]

        # Serial, mapping, ratios (unchanged) ...
        self.port = rc["port"]
        self.baud = int(rc.get("baudrate", 1_000_000))

        self.joint_order = list(rc["joint_order"])
        self.motor_ids   = [int(x) for x in rc["motor_ids"]]
        assert len(self.joint_order) == len(self.motor_ids)

        self.ticks_per_turn = int(rc.get("ticks_per_turn", 4096))

        # Gear ratios
        gr = rc.get("gear_ratios", {})
        self.gear_ratio = {int(k): float(v) for k, v in gr.items()}
        
        # Motor orientations (+1 or -1)
        mo = rc.get("motor_orientations", {})
        self.motor_orientations = {int(k): int(v) for k, v in mo.items()}

        # (Legacy) zero offsets kept for compatibility but NOT used in the new math
        zo = rc.get("zero_offsets_deg", {})
        self.zero_off_rad = {int(k): math.radians(float(v)) for k, v in zo.items()}

        # Optional “position offset” you had before – we keep it, applied last
        po = rc.get("hack_pos_zero_offsets_deg", {})
        self.pos_off = {int(k): float(v) for k, v in po.items()}

        # NEW: Home definition in loops + tick
        ht = rc.get("home_ticks", {})
        hl = rc.get("home_loops", {})
        self.home_ticks = {int(k): int(v) for k, v in ht.items()}
        self.home_loops = {int(k): int(v) for k, v in hl.items()}

        # Precompute home_total_ticks per motor: loops*4096 + tick
        self._home_total_ticks = {
            sid: self.home_loops.get(sid, 0) * self.ticks_per_turn + self.home_ticks.get(sid, 0)
            for sid in self.motor_ids
        }

        # Motion defaults
        self.speed_default = int(rc.get("speed_default", 133))
        self.acc_default   = int(rc.get("acc_default", 50))

        self._speed_min = int(rc.get("speed_min", 1))
        self._speed_max = int(rc.get("speed_max", 4095))    

        # SDK + threading
        self._port = PortHandler(self.port)
        if not self._port.openPort():
            raise RuntimeError(f"Failed to open port {self.port}")
        if not self._port.setBaudRate(self.baud):
            raise RuntimeError(f"Failed to set baudrate {self.baud}")
        self._pkt = sts(self._port)

        self._comm_lock = threading.Lock()
        self._goals_ticks: Dict[int, int] = {}
        self._events: Dict[int, threading.Event] = {}
        self._stop = threading.Event()

        # Seed from current absolute tick and init loop counters
        self._previous_ticks: Dict[int, int] = {}
        self._loop_count: Dict[int, int] = {}

        for sid in self.motor_ids:
            with self._comm_lock:
                self._pkt.ChangeMode(sid, 0)     # position mode
                self._pkt.ChangeMaxLimit(sid, 0) # disable limits if 0 means “none” in your SDK
                self._pkt.ChangeMinLimit(sid, 0)

            cur_ticks = self._safe_read_abs_pos(sid)
            self._goals_ticks[sid] = cur_ticks

            # Initialize loop counters relative to current tick
            self._previous_ticks[sid] = cur_ticks
            self._loop_count[sid] = self.home_loops.get(sid, 0)

            self._events[sid] = threading.Event()

        # Workers
        self._workers = []
        for sid in self.motor_ids:
            t = threading.Thread(target=self._motor_worker, args=(sid,), daemon=True, name=f"motor-{sid}")
            t.start()
            self._workers.append(t)

        log.info(f"[{component_name}] ArkBotDriver initialised on {self.port} @ {self.baud}")

    # ---------------- driver API ----------------

    def pass_joint_positions(self, joints: List[str]) -> Dict[str, float]:
        out: Dict[str, float] = {}
        half = self.ticks_per_turn // 2
        for jname in joints:
            sid   = self._sid_from_joint(jname)
            ticks = self._safe_read_abs_pos(sid)

            raw = ticks - self._previous_ticks[sid]
            if   raw >  half: self._loop_count[sid] -= 1   # wrapped 4095->0
            elif raw < -half: self._loop_count[sid] += 1   # wrapped 0->4095
            self._previous_ticks[sid] = ticks

            total_ticks = self._loop_count[sid] * self.ticks_per_turn + ticks
            home_total  = self._home_total_ticks.get(sid, 0)
            gear        = self.gear_ratio.get(sid, 1.0)
            pos_offset  = self.pos_off.get(sid, 0.0)

            angle = ((total_ticks - home_total) / (self.ticks_per_turn * gear)) * _TWO_PI
            out[jname] = angle - pos_offset
            # print(f"[sid {sid}] ticks={ticks} loops={self._loop_count[sid]} total={total_ticks} -> {out[jname]:.3f} rad")

        return out


    def pass_joint_group_control_cmd(self, control_mode: str, cmd: Dict[str, float], **kwargs) -> None:
        group = kwargs.get("group_name", "arm")
        if control_mode != "position":
            log.warn(f"Only position mode is implemented; ignoring control_mode={control_mode} for group {group}")
            return

        for jname, target_rad in cmd.items():
            sid = self._sid_from_joint(jname)
            goal_total = self._angle_rad_to_total_ticks(sid, float(target_rad))
            
            self._goals_ticks[sid] = int(round(goal_total))
            self._events[sid].set()

            # Debug:
            print(f"[sid {sid}] θ={target_rad:.3f} rad -> total={goal_total:.1f} ticks -> send={goal_total}")

        time.sleep(0.001)

    # ---------------- helpers ----------------

    def _angle_rad_to_total_ticks(self, sid: int, angle_rad: float) -> float:
        """goal_total_ticks = home_total_ticks + angle_rad * (ticks_per_turn / 2π) * gear_ratio - (pos_offset in ticks)"""
        gear = float(self.gear_ratio.get(sid, 1.0))
        home_total = float(self._home_total_ticks.get(sid, 0))
        pos_offset = float(self.pos_off.get(sid, 0.0))
        ori = self.motor_orientations.get(sid, 1)
        motor_mech_angle = (angle_rad + pos_offset) * float(ori)
        # desired mechanical angle *from home*, expressed in ticks on the *motor* side
        mech_ticks = (motor_mech_angle * (self.ticks_per_turn / _TWO_PI)) * gear
        return home_total + mech_ticks

    def _safe_read_abs_pos(self, sid: int) -> int:
        with self._comm_lock:
            val = self._pkt.ReadAbsPos(sid)
        return 0 if val is None else int(val)
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

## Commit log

2025-10-06 Inital Move
    [ark_bot.urdf]
2025-10-06 3D models
    [Base Bearing Cover.step, Base Motor Holder.step, Base.step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]
2025-10-06 Excel list of models
    [List of all 3D models and BOM.xlsx]
2025-10-13 Added Assembly Video
    Added an image which can be clicked to direct you to the video. and added a link which also works
